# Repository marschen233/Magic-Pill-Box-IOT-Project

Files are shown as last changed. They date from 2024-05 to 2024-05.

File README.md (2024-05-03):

    * Author: Haowei Chen
    * Co-Author: Pin-Yi Yu
    * Description of hardware: (windows, Adafruit 938 OLED Screen with I2C Interface, SAMW25 Module, Force Sensor with I2C Interface, Temprature/Humidity Sensor sensor with I2C, Electromagnetic Locking Lid with Spring Open Mechanism, buck converter, boost converter) 

## 1. Video Presentation

- [Video Presentation](https://youtu.be/nQqyR8lDyXY?si=AE45nUH7O6IaNKej)

## 2. Project Summary

### Device Description

- The Magic Pill Box is designed to help elderly people who are not familiar with phone and tablet devices to aid their medication. The solution is using an IOT device and remote access. 

### Inspiration

- My grandparents are diagnosed with high blood pressure and are taking medicine on a daily basis. However, they keep forgetting to take the pills. First, me and my parents would give them a call to remind them, and they still forget to take the pill after hanging up the phone. We eventually bought them a smart pill box, but they are not so familiar with the setup, and still not working as we expected. This is when I came up with the idea of Magic Pill Box. 

### Device Functionality

- The Magic Pill Box is made with a few interesting functions. First of all, the safe lock function which is integrated with 3 electric magnets and a buzzer. When the buzzer is beeping, it reminds the user to take the pill and based on the number on the OLED screen, the user will need to take the pills from the corresponding compartment. Before taking the pills, the user needs to press the switch to open the compartment by unlocking the electric magnets. Once the user eats the pills and closes the lid, the lid will then press the button sticked inside the compartment and shut off the buzzer. 

- The Magic Pill Box is also equipped with the SHTC3 temperature and humidity sensor, and the purpose is to monitor the storage condition. If there's an anonymous reading, the buzzer will start beeping and send the user a notification that the storage condition is dangerous to the medicine.

- The user can use the node-red system to set up the alarm schedule and change the storage condition threshold.

### Challenges

- There are many challenges during the development. The first challenge we ran into was debugging the hardware issue, which had something to do with the component on the circuit board. For example, we were stuck on the I2C device development for almost 2 weeks and turned out to be a pin mapping error. The second challenge was developing firmware. Since we needed to write all freeRTOS drivers to our sensors, it took us a while to test and debug. The last challenge was casework design. I spent a lot of time on modifying the 3D design of the casework and had to print multiple prototypes to test the device and printing something out really took a lot of time. 

### Prototype Learnings

- The biggest lesson I learned from this project was to start things early and avoid sudden changes in design. The other thing I think we can improve is start casework design based on the firmware, and not the other way around. I spent a lot of time on how to make a perfect casework to fit my hardware, and in the end, it turned out there were lots of things that needed to be modified.

### Next Steps

- In the future, I am planning a two-phase update on this device using over-the-air updates. First, I want to add more information to the screen(time/temperature/humidity). Next, I will add a UI function in which the user can set the schedule and change the storage condition threshold directly on the user interface. 

## 3. Code and Design

## 4. Project Photos & Screenshots

### Casework

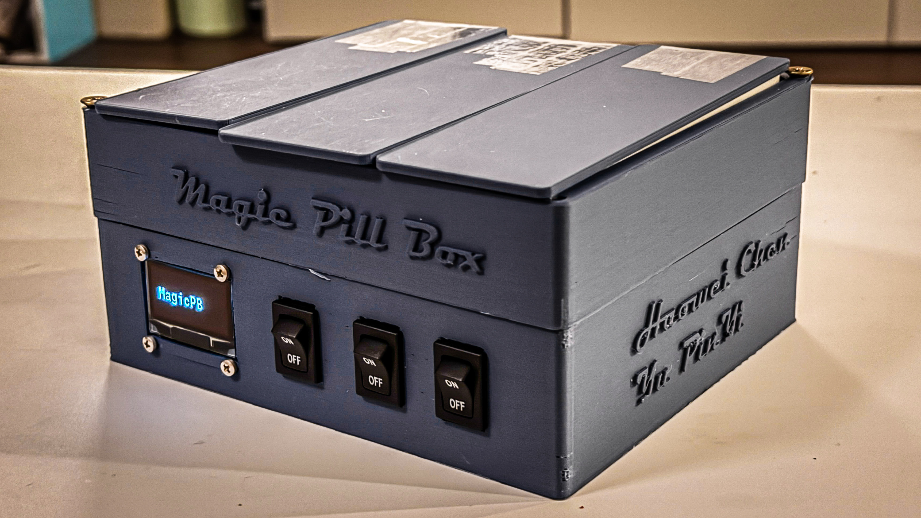
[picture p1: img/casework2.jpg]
Casework
- 
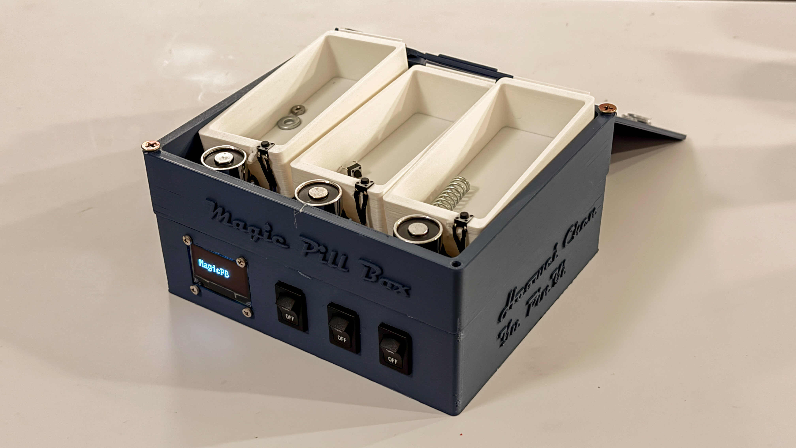
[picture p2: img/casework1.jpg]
Casework
- 

### a. The standalone PCBA, top

- PCBA Top View

### b. The standalone PCBA, bottom

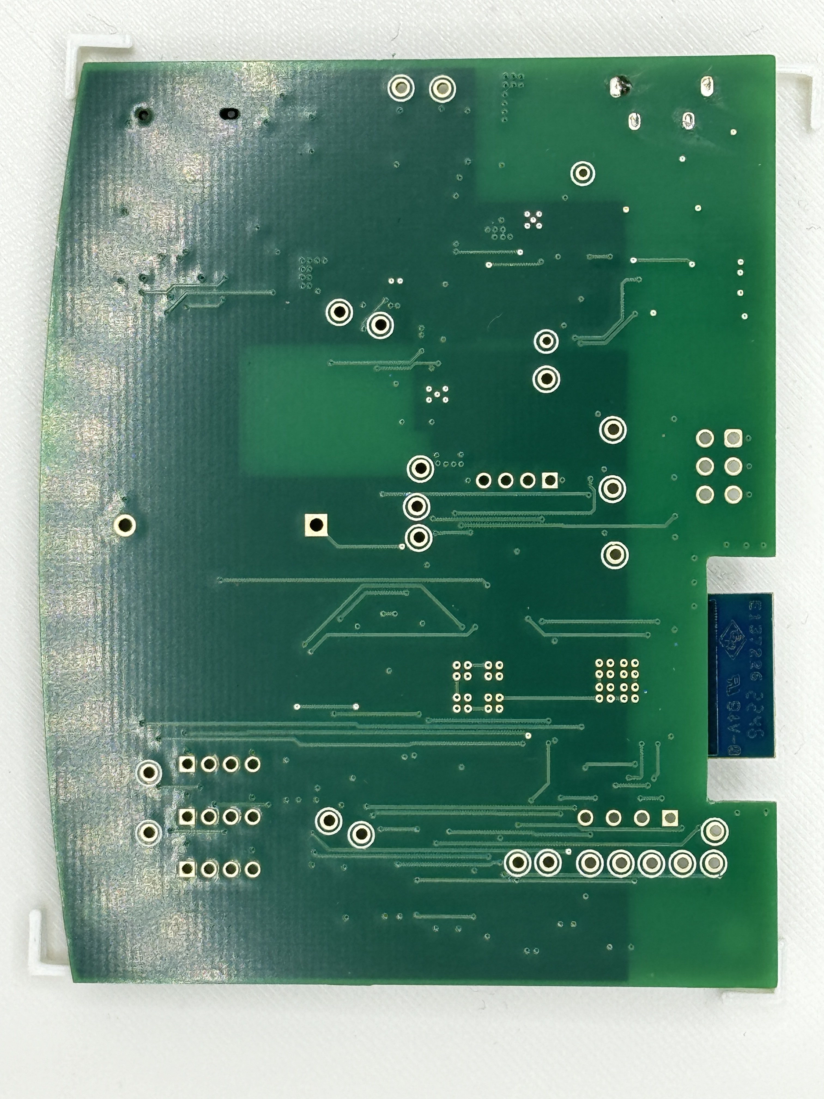
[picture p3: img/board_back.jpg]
PCBA Top View
- 

### c. Thermal camera images while the board is running under load 

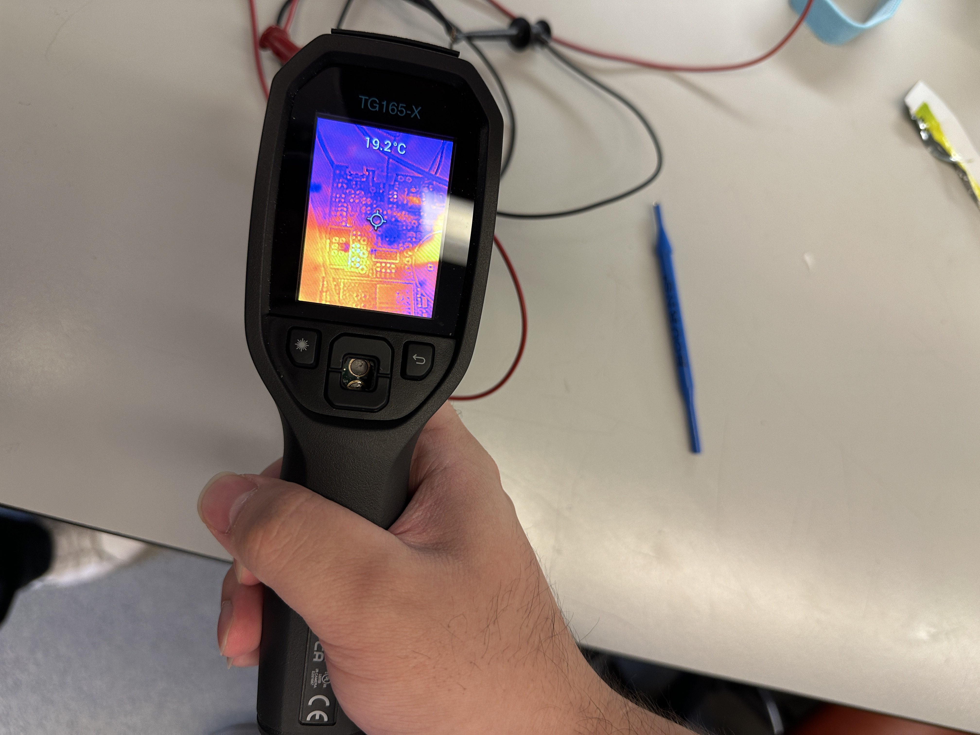
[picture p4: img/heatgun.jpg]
Thermal Image
- 

### d. The Altium Board design in 2D view

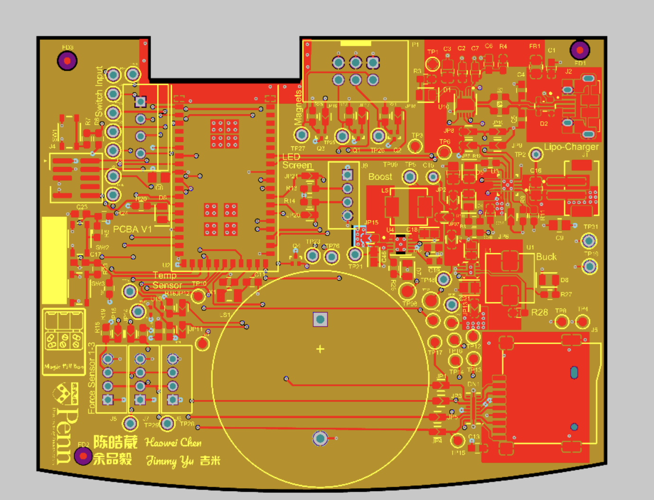
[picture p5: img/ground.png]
Ground Plane View
- 
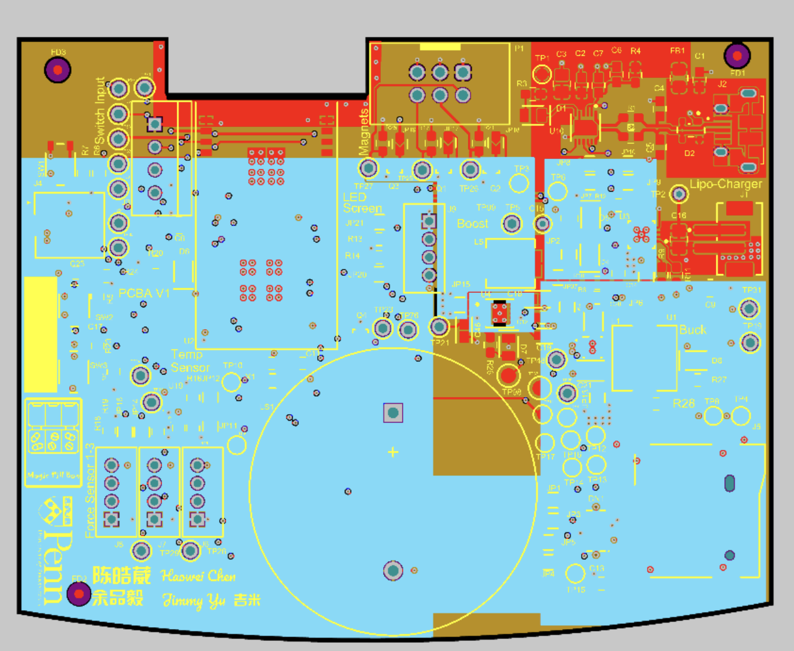
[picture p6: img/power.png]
Power Plane View
- 

### e. The Altium Board design in 3D view

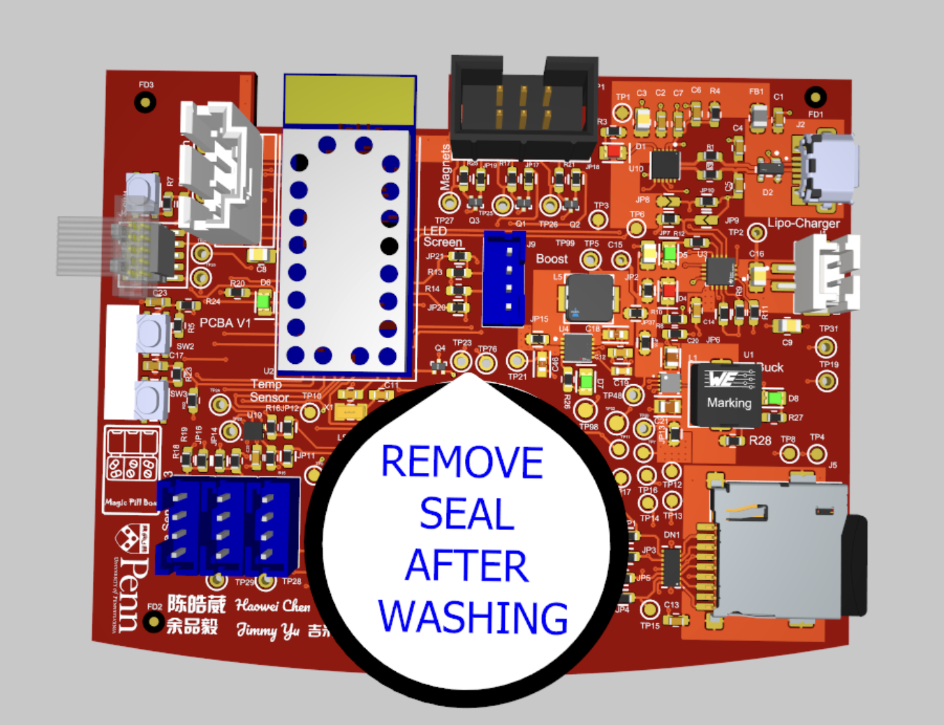
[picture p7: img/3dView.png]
3D View
- 

### f. Node-RED dashboard

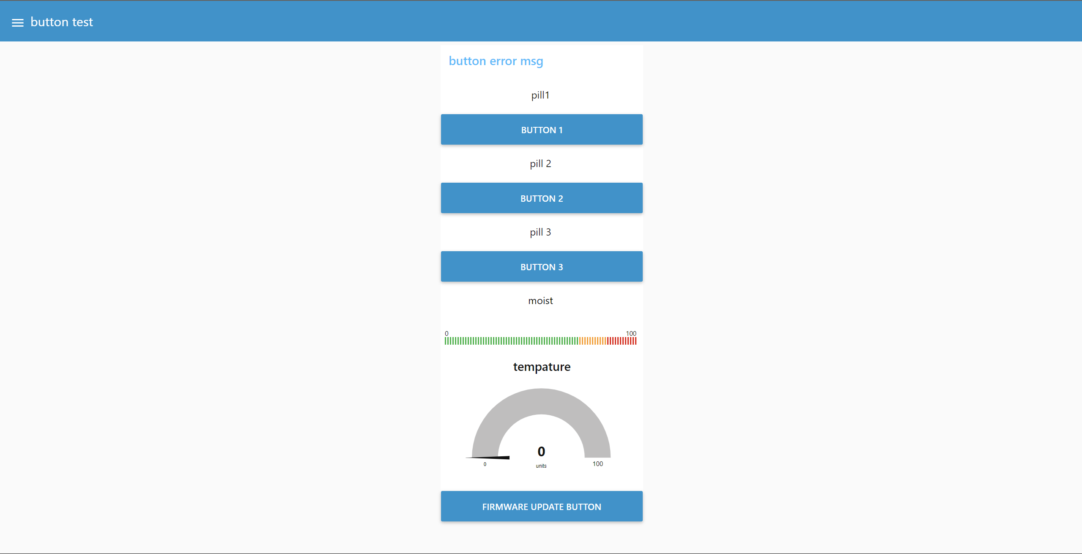
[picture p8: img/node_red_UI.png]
Node-Red Dashboard
- 

### g. Node-RED backend

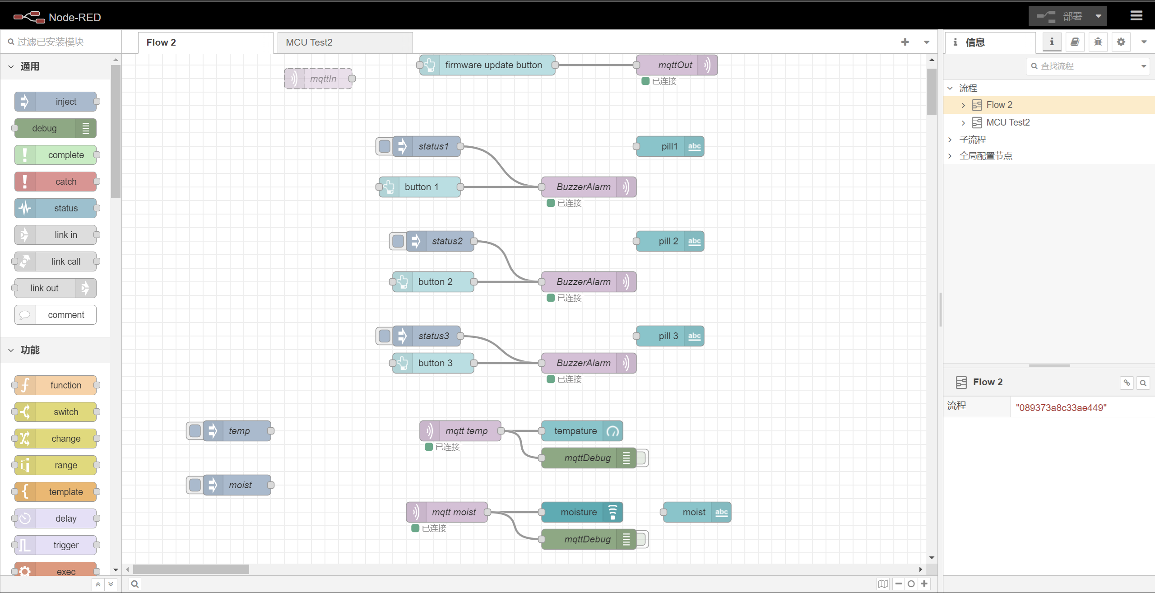
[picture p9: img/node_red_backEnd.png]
Node-Red Backend
- 

### h. Block diagram

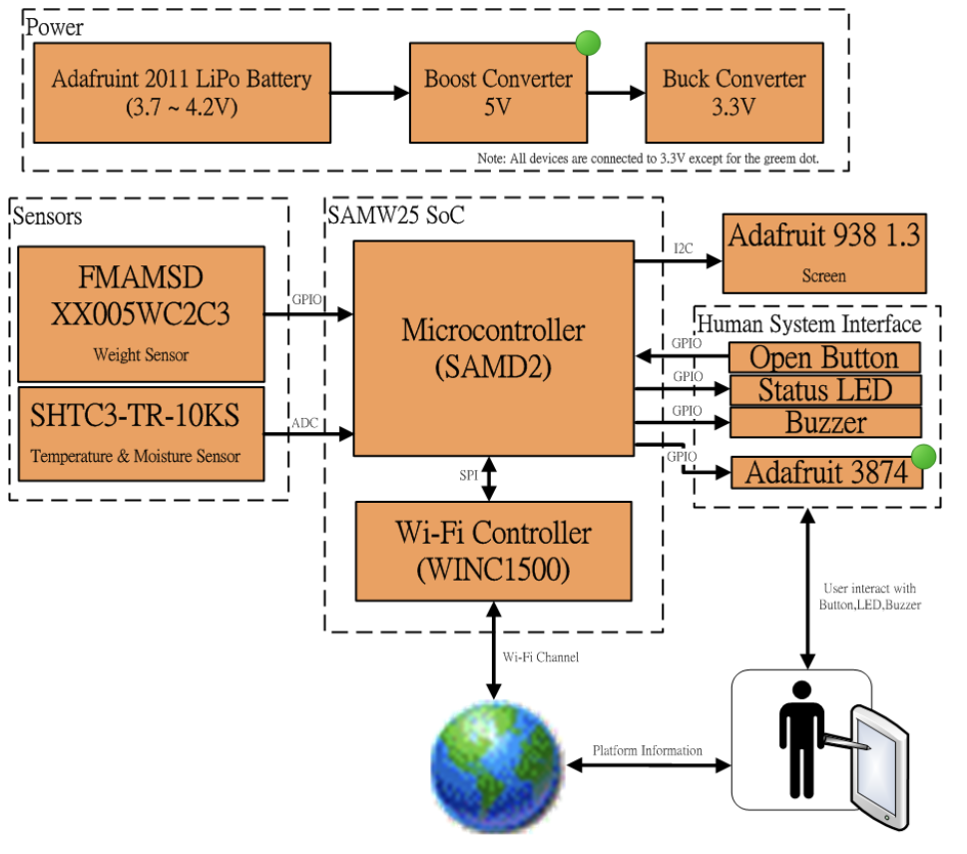
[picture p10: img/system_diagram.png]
Block Diagram
- 
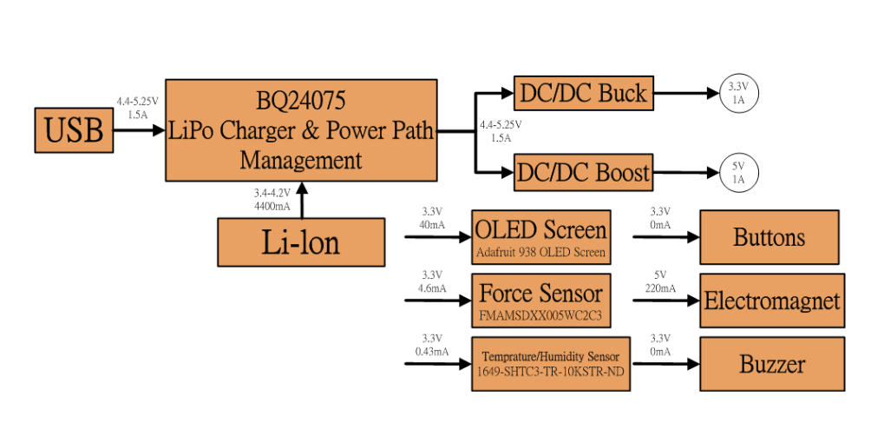
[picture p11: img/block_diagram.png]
Block Diagram
-

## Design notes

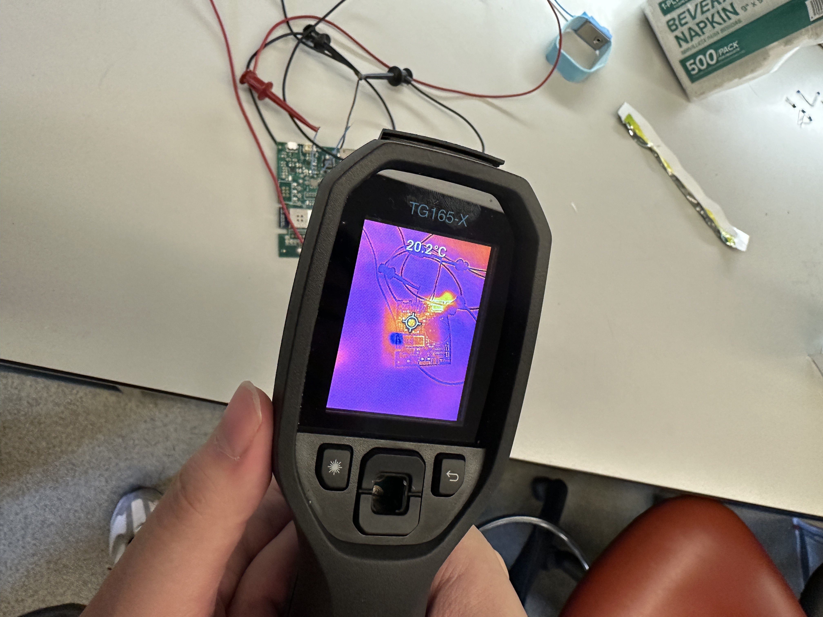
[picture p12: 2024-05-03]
img/thermalgun.jpg

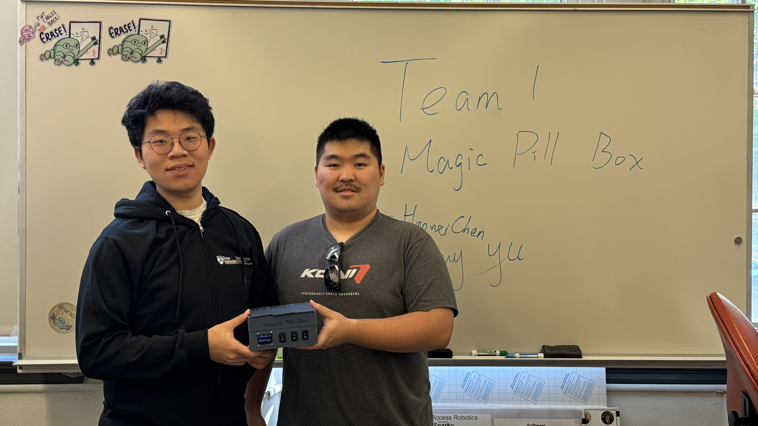
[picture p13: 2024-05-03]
img/teamphoto.jpg

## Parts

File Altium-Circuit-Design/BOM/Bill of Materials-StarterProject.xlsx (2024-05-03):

Line # | Name | Description | Designator | Quantity | Manufacturer 1 | Manufacturer Part Number 1 | Manufacturer Lifecycle 1 | Supplier 1 | Supplier Part Number 1 | Supplier Unit Price 1 | Supplier Subtotal 1
3 | CAP 0603 0.01UF 16V 10% X7R | Capacitor Surface Mount 0603 Footprint 0.01UF 16V 10% Tolerance Ceramic X7R | C1 | 1 | Yageo | CC0603KRX7R7BB103 | Volume Production | Digikey | 311-3369-1-ND | 0.1 | 0.1
2 | CAP 0603 0.1UF 16V 10% X7R | Capacitor Surface Mount 0603 Footprint 0.1UF 16V 10% Tolerance Ceramic X7R | C2, C6, C7, C13, C22 | 5 | Yageo | CC0603KRX7R9BB104 | Volume Production | Digikey | 311-1344-1-ND | 0.1 | 0.5
4 | CAP 0805 4.7UF 16V 10% X7R | Capacitor Surface Mount 0805 Footprint 4.7UF 16V 10% Tolerance Ceramic X7R | C3, C15, C16 | 3 | Yageo | CC0805KKX7R7BB475 | Volume Production | Digikey | 311-1883-1-ND | 0.39 | 1.17
5 | CAP 0603 47PF 50V 5% C0G | Capacitor Surface Mount 0603 Footprint 47PF 50V 5% Tolerance Ceramic C0G | C4, C5 | 2 | Yageo Phycomp | CC0603JRNPO9BN470 | Volume Production | Digikey | 311-1065-1-ND | 0.1 | 0.2
6 | CAP 0805 10UF 16V 20% X7R | Capacitor Surface Mount 0805 Footprint 10UF 16V 20% Tolerance Ceramic X7R | C8, C9 | 2 | Yageo | CC0805KKX5R7BB106 | Volume Production | Digikey | 311-1865-1-ND | 0.35 | 0.7
8 | CAP 0603 18PF 50V 5% C0G | Capacitor Surface Mount 0603 Footprint 18PF 50V 5% Tolerance Ceramic C0G | C10, C11 | 2 | Yageo | CC0603JRNPO9BN180 | Volume Production | Digikey | 311-1061-1-ND | 0.1 | 0.2
7 | CAP 0603 1UF 16V 10% X7R | Capacitor Surface Mount 0603 Footprint 1UF 16V 10% Tolerance Ceramic X7R | C12, C14, C17, C23 | 4 | Yageo | CC0603KRX7R7BB105 | Volume Production | Digikey | 311-1446-1-ND | 0.1 | 0.4
 | C1608X5R1A106M080AC | Multilayer Ceramic Capacitors 10μF ±20% 10V X5R SMD 0603 | C18, C46 | 2 | TDK | C1608X5R1A106M080AC | Not Recommended for New Design | Digikey | 445-6853-6-ND | 0.44 | 0.88
 | CC0603KRX7R7BB103 | CAP CER 10000PF 16V X7R 0603 | C19 | 1 | Yageo | CC0603KRX7R7BB103 | Volume Production | Arrow Electronics | CC0603KRX7R7BB103 | 0.0038 | 0.0038
 | C0805C106K9PACTU | CAP CER 10UF 6.3V X5R 0805 | C20 | 1 | KEMET | C0805C106K9PACTU | Volume Production | Mouser | 80-C0805C106K9P | 0.14 | 0.14
 | GRM21BD70J226ME44L | Chip Multilayer Ceramic Capacitors for General Purpose, 0805, 22uF, X7T, +22%/-33%, 20%, 6.3V | C21 | 1 | Murata | GRM21BD70J226ME44L | Volume Production | Digikey | 490-14659-1-ND | 0.46 | 0.46
10 | LSM0805412V | Single Color LED, RED, 0805 | D1, D4 | 2 | Visual Communications | LSM0805412V | Volume Production | Digikey | 28-LSM0805412VCT-ND | 0.53 | 1.06
9 | PRTR5V0U2X,215 | Trans Voltage Suppressor Diode, 5.5V V(RWM), Unidirectional, 1 Element, Silicon | D2 | 1 | Nexperia | PRTR5V0U2X,215 | Volume Production | Digikey | 1727-3884-1-ND | 0.42 | 0.42
11 | LSM0805452V | Single Color LED, Green, 0805 | D5, D6, D7, D8 | 4 | Visual Communications | LSM0805452V | Volume Production | Digikey | 28-LSM0805452VCT-ND | 0.39 | 1.56
12 | ECLAMP2410PQTCT | Trans Voltage Suppressor Diode, 5V V(RWM), Bidirectional, 7 Element, Silicon with EMI Filter | DN1 | 1 | Semtech | ECLAMP2410PQTCT | Volume Production | Rochester Electronics | ECLAMP2410PQTCT | 0.6418 | 0.6418
13 | BLM21PG221SN1 | Ferrite Chip 2000 mA 220 Ohms Differential Mode - Single 0805 Footprint | FB1 | 1 | Murata | BLM21PG221SN1 | Volume Production | SHENGYU ELECTRONICS | BLM21PG221SN1 | 0.012 | 0.012
 | B2B-PH-SM4-TBT(LF)(SN) | Connector Header, PH Series, 2 Position, 2.00mm, 100V, Surface Mount, Solder, Pick and Place, Natural. | J1 | 1 | JST | B2B-PH-SM4-TBT | Unknown | Digikey | 455-B2B-PH-SM4-TBTCT-ND | 0.81 | 0.81
14 | 10103592-0001LF | Conn Micro USB 2.0 Type B RCP 5 POS 0.65mm Solder RA SMD 5 Terminal 1 Port T/R | J2 | 1 | Amphenol ICC / FCI | 10103592-0001LF | Unknown | Mouser | 649-10103592-0001LF | 0.67 | 0.67
 | 5-104363-3 | Board Connector, 4 Contact(s), 1 Row(s), Male, Straight, 0.1 inch Pitch, Solder Terminal, Locking, Black Insulator, Plug | J3 | 1 | TE Connectivity | 5-104363-3 | Volume Production | Mouser | 571-5-104363-3 | 1.35 | 1.35
15 | ARM Cortex Debug | 10 Pin Shrouded Header, 0.050", Key Pin 7 | J4 | 1 | Samtec | FTSH-105-01-F-DV-007-K-P | Volume Production | Mouser | 200-FTSH1051FDV007KP | 4.01 | 4.01
16 | 693071020811 | WR-CRD Micro SD Card Connector Push & Push | J5 | 1 | Wurth Electronics | 693071020811 | Volume Production | Mouser | 710-693071020811 | 3.96 | 3.96
 | B4B-PH-K-S(LF)(SN) | Connector Header, PH Series, 4 Position, 2.00mm, Solder, Through Hole, Tin, Natural | J6, J7, J8, J9 | 4 | JST | B4B-PH-K-S(LF)(SN) | Volume Production | Classic Components | B4B-PH-K-S(LF)(SN) | 0.038 | 0.152
 | 0603 link | 0O link, SMD, 0603, Solder Bridge Option | JP36, JP37 | 2 | Stackpole Electronics | RMCF0603ZT0R00 | Volume Production | Digikey | RMCF0603ZT0R00CT-ND | 0.013 | 0.13
 | 744311100 | General Purpose Inductor, 1uH, 20%, 1 Element, SMD, 2827 | L1 | 1 | Wurth Electronics | 744311100 | Volume Production | Digikey | 732-4177-1-ND | 3.8 | 3.8
 | IHLP2020BZER1R0M11 | Fixed Inductors Commercial Low DCR Series 1uH 7.5A 18.1mΩ 20% | L5 | 1 | Vishay Dale | IHLP2020BZER1R0M11 | Volume Production | Mouser | 70-IHLP2020BZER1R0M1 | 1.12 | 1.12
 | AST-03208MR-R | 8 Ohms General Purpose Speaker 100 mW 500 Hz ~ 20 kHz Top Round | LS1 | 1 | Projects Unlimited | AST-03208MR-R | Unknown | Mouser | 665-AST-03208MR-R | 2.7 | 2.7
 | 61200621621 |  | P1 | 1 | Wurth Electronics | 61200621621 | Volume Production | Digikey | 732-5394-ND | 0.48 | 0.48
 | RE1E002SPTCL | MOSFET P-CH 30V 0.25A EMT3 | Q1, Q2, Q3, Q4 | 4 | Rohm | RE1E002SPTCL | Volume Production | Mouser | 755-RE1E002SPTCL | 0.34 | 1.36
18 | RES 0603 27 1% | Resistor Surface Mount, 27 Ohms, 0603 Footprint, 1% Tolerance 0.1W | R1, R2 | 2 | Stackpole Electronics | RMCF0603FT27R0 | Volume Production | Digikey | RMCF0603FT27R0CT-ND | 0.015 | 0.15
19 | RES 0603 1K 1% | Resistor Surface Mount, 1K Ohms, 0603 Footprint, 1% Tolerance 0.1W | R3, R4, R10, R11, R12, R20, R26, R27 | 8 | Stackpole Electronics | RMCF0603FT1K00 | Volume Production | Digikey | RMCF0603FT1K00CT-ND | 0.015 | 0.15
22 | RES 0603 100 1% | Resistor Surface Mount, 100 Ohms, 0603 Footprint, 1% Tolerance 0.1W | R5, R7, R23 | 3 | Stackpole Electronics | RMCF0603FT100R | Volume Production | Digikey | RMCF0603FT100RCT-ND | 0.015 | 0.15
20 | RES 0603 10K 1% | Resistor Surface Mount, 10K Ohms, 0603 Footprint, 1% Tolerance 0.1W | R6, R13, R14, R15, R16, R17, R18, R19, R21, R22, R24, R25 | 12 | Stackpole Electronics | RMCF0603FT10K0 | Volume Production | Digikey | RMCF0603FT10K0CT-ND | 0.015 | 0.18
23 | RES 0603 1.13K 1% | Resistor Surface Mount, 1.13K Ohms, 0603 Footprint, 1% Tolerance 0.1W | R8, R9 | 2 | Stackpole Electronics | RMCF0603FT1K13 | Volume Production | Digikey | RMCF0603FT1K13CT-ND | 0.015 | 0.15
 | RES 0603 178K 1% | Resistor Surface Mount, 178K Ohms, 0603 Footprint, 1% Tolerance 0.1W | R28 | 1 | Stackpole Electronics | RMCF0603FT178K | Volume Production | Quest | RMCF0603FT178K | 0.009 | 0.009
100 | PTS810SJK250SMTRLFS | Keypad Switch, 1 Switches, SPST, Momentary tactile button, 0.05A, 16VDC, 3.23N, Solder Terminal, Surface Mount-straight | SW1, SW2, SW3 | 3 | ITT C&K | PTS810SJK250SMTRLFS | Volume Production | Digikey | CKN10503CT-ND | 0.34 | 1.02
 | TPS62082DSGR | Buck Step Down Regulator with 2.3 to 6 V Input and 3.3 V Output, -40 to 85 degC, 8-Pin WSON (DSG), Green (RoHS & no Sb/Br) | U1 | 1 | Texas Instruments | TPS62082DSGR | Volume Production | Mouser | 595-TPS62082DSGR | 1.64 | 1.64
25 | ATSAMW25H18-MR210 | WiFi 802.11b/g/n Transceiver Module 2.412GHz ~ 2.484GHz Integrated, Trace Surface Mount, Integrated SAMD21 Cortex M0+ | U2 | 1 | Microchip | ATSAMW25H18-MR210PB | Volume Production | ICSOSO Electronics Company Limited | ATSAMW25H18-MR210PB | 14.37 | 14.37
 | BQ24075RGTR | Power Supply Support Circuit, Adjustable, 1 Channel, 6.6, PQCC16 | U3 | 1 | Texas Instruments | BQ24075RGTR | Volume Production | Digikey | 296-38874-6-ND | 2.35 | 2.35
 | TPS61232DRCR | IC REG BOOST 5V 4A 10VSON | U4 | 1 | Texas Instruments | TPS61232DRCR | Volume Production | Digikey | 296-44498-1-ND | 2.74 | 2.74
24 | FT234XD-R | USB Bridge, USB to UART USB 2.0 UART Interface 12-DFN (3x3) | U10 | 1 | FTDI | FT234XD-R | Volume Production | Digikey | 768-1178-1-ND | 2.26 | 2.26
 | SHTC3-TR-10KS |  | U19 | 1 | Sensirion | SHTC3-TR-10KS | Unknown | Digikey | 1649-SHTC3-TR-10KSCT-ND | 2.76 | 2.76
27 | ABS07-32.768KHZ-T | Crystal 32.768kHz ±20ppm (Tol) 12.5pF FUND 70kΩ 2-Pin CSMD T/R | X1 | 1 | Abracon | ABS07-32.768KHZ-T | Volume Production | Mouser | 815-ABS07-32.768KHZT | 0.62 | 0.62

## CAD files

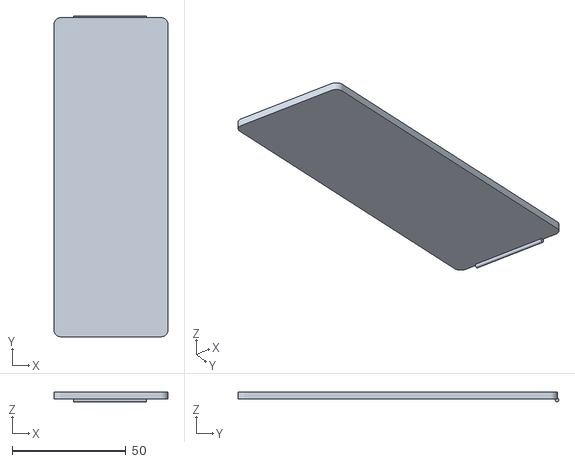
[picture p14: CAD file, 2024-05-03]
3d-part/516_LID.stl
50.0 x 140.6 x 4.30

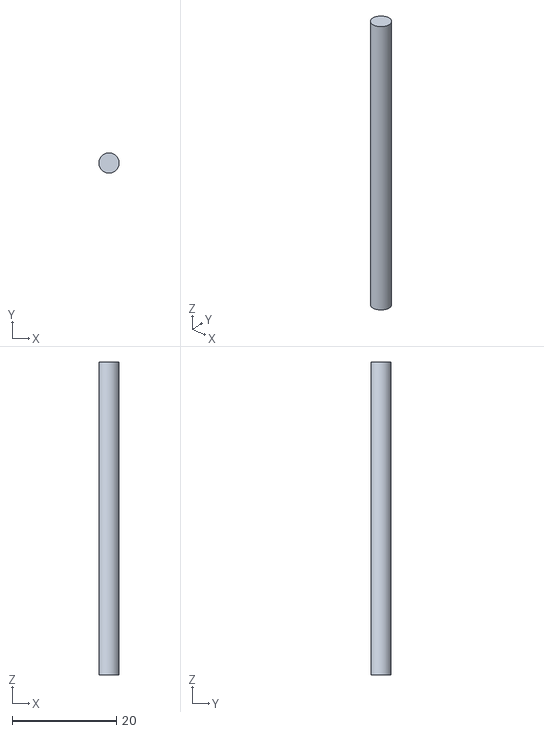
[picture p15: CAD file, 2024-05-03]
3d-part/final_connector.stl
3.90 x 3.90 x 60.0

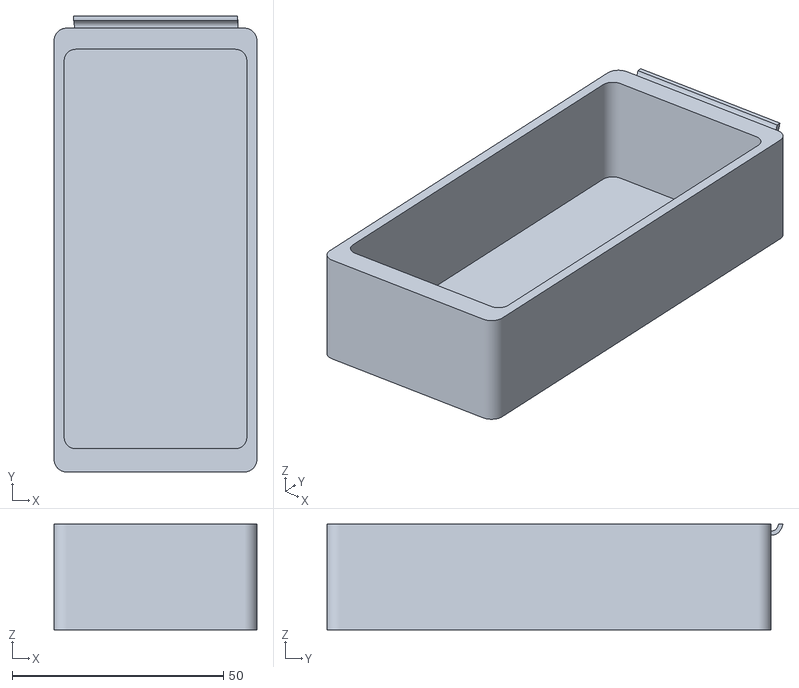
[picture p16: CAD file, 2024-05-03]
3d-part/516_pill_box.stl
48.0 x 107.9 x 25.0

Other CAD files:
3d-part/516_part_base.stl
